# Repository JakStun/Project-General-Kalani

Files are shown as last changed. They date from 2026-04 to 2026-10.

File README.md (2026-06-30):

# Project-General-Kalani-V1

A talking and moving bust of an ST-series military strategic analysis and tactics droid serving the Confederacy of Independent Systems.

## Warning

* The neck joint is currently non-functional.

## Architecture Preview

```
User → Microphone → Raspberry Pi → Server → Response → Speaker
```

## Components

* Raspberry Pi 4 (4 GB)
* 3× RGB LED Module (7× NeoPixel WS2812)
* Adafruit I2S MEMS Microphone Breakout – SPH0645LM4H
* JBL Speaker
* LD2410C Human Presence Sensor (HLK-LD2410C)
* PCA9685 Servo Controller
* 2× Waveshare MG90S Micro Servos
* MG996R Servo
* External battery capable of powering the servos
* Dupont cables (10 cm, 20 cm, 30 cm, and 40 cm)

### Stores

* https://rpishop.cz
* https://www.drotik-elektro.sk

---

## Head

* All parts were printed on a Prusa Mini+.
* The parts were sanded using 120 → 240 → 320 → 600 grit sandpaper.
* Before using the 320 and 600 grit sandpaper, I applied a thin coat of Modulan 101 wood filler (purchased from Hornbach). It creates a smooth surface, hides the visible 3D printing layers, dries quickly, and does not chip off. Need to add little bit of water and mix it up.

### Filaments

* Prusament PETG Pigment White
* Buddy3D PLA White
* PolyTerra PLA White

### Stores

* https://www.prusa3d.com

* https://www.3djake.sk

* Printing all components took approximately three weeks. (It could have been faster—I wasn't printing continuously.)

* Approximately 1.5 spools of filament were used.

---

## Paints

* MASTON Plastic Primer
* MASTON Metallic Black
* MASTON Metallic Silver

### Store

* https://www.hornbach.sk

---

## Updates

Progress photos can be found in the `updates` folder.

---

## Project Preview

<p align="center">
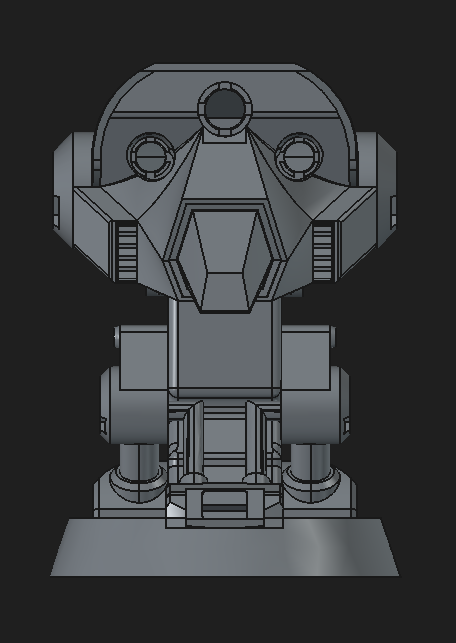
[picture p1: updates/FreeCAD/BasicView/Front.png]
Project Preview
  
</p>

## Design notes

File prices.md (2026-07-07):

# Cost of this project:

- Servos: 26 e (MG90S 180, MG996 180)
- MIC: 18 e (I bought second one for stereo and as a backup)
- Wiring: ~ 5 e
- Sensors: 30 e (LD2410, LD2410C, LD2450) (one LD2410C sensor self-combusted for some reason, had to buy new one...)
- RPi Camera V2: 16.5 e (testing human recognition)
- Adafruit 4 Ω 3 W Speakers - 10 e
- MAX98357 I2S mono amplifier 3W - 10 e (2x)
- LEDS: ~ 20 e (various types)

- TOTAL COST: 135.5 euros

- price is even higher though, these are just things I needed to buy. 

Components used, but not listed: 
- RPi 4 4GB (variable price nowadays)
- microSD 32GB (~10-15 euros)
- JBL Flip 3 (???)
- Old chinese powerbank (???)
- micro soldering station + other helper components (~90 euros)

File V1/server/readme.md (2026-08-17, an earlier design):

# Lucrehulk

- brain of all operations that require thinking/analysis

Run this command if you want all devices on local network to send requests:
```uvicorn main:app --host 0.0.0.0 --port 8000```

## Installation:

Tricky install-> torch (check newer versions), for this project I used: torch==2.6.0+cu124
Install it like this:  ```python.exe -m pip install torch==2.6.0+cu124 torchaudio==2.6.0+cu124 --index-url https://download.pytorch.org/whl/cu124```

For faster-wisper to work you need to have Visual Studio Build Tools for C++ installed (https://visualstudio.microsoft.com/visual-cpp-build-tools/)
Only then install: ```pip install "faster-whisper==1.2.1"```

After these are installed, install: ```pip install -r requirements.txt```

CUDA Tests (if available):
```python -c "import torch; print(torch.__version__); print(torch.version.cuda); print(torch.cuda.is_available()); print(torch.cuda.get_device_name(0))"```

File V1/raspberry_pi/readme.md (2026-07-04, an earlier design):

# V1 - Chilion Mahlon

## Full Cycle Preview:

```
I.   Human comes in front of Servitor (< 55 cm)

II.   Servitor activates itself, because it listens to LD2410S radar, that uncovers every movement in front of it:
        - servo moves head into 'awake' position
        - LEDs activate through startup  animation
        - MIC is set to active (NOT recording yet)
        - Optional: Servitor says something along these lines: At your service, Your word is my command...

III.  Human speaks Servitors name, thus activating MIC -> LEDs change color to Listening Mode

IV.   After humans request is recorded (human stops speaking and there is a slight/noticable pause), servitor sends their request for wisdom to Lucrehulk (Main Cogitator) and initiates Processing Mode, LEDs change to signal change

V.    Lucrehulk processes request for knowledge and returns appropriate answer to servitor (for more knowledge about Lucrehulk seek server folder)

VI.   Servitor spreads the unknown misterious knowledge to the keen listener and initiates Preaching Mode, again LEDs indicate this change

VII.  Human, satisfied with this new wisdom leaves servitor

VIII. After sensing no activity for a long time (~5 mins) Servitor starts 'sleep' funcs to preserve power and prepares itself for slumber: 
        - servo moves to 'sleep' position
        - LEDS start to jitter and at the end shut down
        - MIC is set to off
```

---

## Before launching code (Cerebrum.py):

- Interface Options (```sudo raspi-config```):
    - enable I2S (needed for MIC, it's not here anymore on newer version, just change config.txt)
    - enable I2C (needed for PCA9685)
    - enable SPI (needed for LED Control)
    - Serial Port (needed for LD2410 sensor):
        - disable ligin shell over serial
        - enable serial hardware

- MIC Configuration setup:
    I. ```sudo nano /boot/firmware/config.txt```
    II. Add/uncomment:
        - ```dtparam=i2s=on```
        - ```dtoverlay=googlevoicehat-soundcard```
    III. sudo reboot
    IV. Check if MIC is recognised and record test audio:
        - ```arecord -l```
        - ```arecord -D hw:3,0 -f S32_LE -r 48000 -c2 test.wav``` (if it doesn't work change hw:...,... -> maybe different port, can be seen by using func above)
        - speak into MIC
        - Ctrl+C -> stop recording
        - test.wav is created in /pi

- Speaker Configuration setup (JBL Flip):
    I. ```sudo systemctl start bluetooth```
    II. ```sudo systemctl enable bluetooth```
    III. ```bluetoothctl``` -> inside it:
        ```power on```
        ```agent on```
        ```default-agent```
        ```scan on``` -> search for XX:XX:XX:XX:XX:XX JBL Flip 3 (don't forget to start bluetooth on speaker aswell)
        ```pair XX:XX:XX:XX:XX:XX``` -> after success, should also see a popup: connection successful
        ```trust XX:XX:XX:XX:XX:XX```
        ```connect XX:XX:XX:XX:XX:XX```
        ```exit```
        
    IV. ```pactl list short sinks or wpctl status``` (depends on system) -> verify audio output, should be already default audio output (has * before name)
    V. ```speaker-test -c2``` or ```pw-play /usr/share/sounds/alsa/Front_Center.wav``` -> you should a stomp sound

    - if there is an error in bluetoothctl, check:
        - ```sudo systemctl status bluetooth --no-pager```
        - ```rfkill list```
        - ```hciconfig -a```
        - ```sudo rfkill unblock bluetooth```
        - ```sudo systemctl restart bluetooth```
        -> try running ```bluetoothctl``` and its commands again, should work now

---

## Installing new packages:

- WRONG APPROACH: sudo pip install --break-system-packages ... -> can break system
- CORRECT APPROACH: .venv (more stable) -> pip install ...

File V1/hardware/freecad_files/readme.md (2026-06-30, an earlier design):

##Warning:
-> FreeCAD files (for prototype and V1) are unfortunately corrupted for FreeCAD 1.1 and can't be opened without getting 10s of errors and warnings
-> They were designed in FreeCAD 1.0.1 - stable to open in this version

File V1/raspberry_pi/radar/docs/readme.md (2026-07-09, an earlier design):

During development, I've tried multiple Hi-Link radar sensors, here are links to offical drives
Only sensor I didn't try out was LD2461 (couldn't find it anywhere to buy it), seems interesting...

LD2410:
https://drive.google.com/drive/folders/1lCQv3mfHJ3XKXzweeHPFnJ_8_D_EWEKk

LD2410B:
https://drive.google.com/drive/folders/16zI-fium_BZeP08EyQke0rWp0BJTMvw3

LD2410C:
https://drive.google.com/drive/folders/1ypOlacBmmFXY6lDQ0f1hEJFmczNe-0WG

LD2450:
https://drive.google.com/drive/folders/1kTt0Z3hjKKrIF3OCIDGdwQ4KotDJ8SGA

LD2461:
https://drive.google.com/drive/folders/14_KgZpL4Th2LTRuq_W0X_ePjHu_Z6lcS

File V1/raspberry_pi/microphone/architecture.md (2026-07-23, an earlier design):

# Microphone Architecture

Used MIC: Adafruit I2S MEMS microphone breakout - SPH0645LM4H

```
microphone_control.py   -> main Controller for mic
recorder.py             -> captures PCM frames
vad.py                  -> voice activity detection
wakeword.py             -> OpenWakeWord wrapper
audio_buffer.py         -> ring buffer
```

Idea: 
First detect speech -> wake word - for that to work, I need MIC to record from the moment the robot is 'up'
    - this will be handled by recorder.py -> returns PCM frames (~ 33 frames per second)

Because of my beginner skills I needed to mostly rely on AI...
Nevertheless I read the docs to each library I used in MIC architecture

docs:
- https://python-sounddevice.readthedocs.io/en/0.5.3

0 vc4-hdmi-0: MAI PCM i2s-hifi-0 (hw:0,0), ALSA (0 in, 2 out)
1 bcm2835 Headphones: - (hw:2,0), ALSA (0 in, 8 out)
2 snd_rpi_googlevoicehat_soundcar: Google voiceHAT SoundCard HiFi voicehat-hifi-0 (hw:3,0), ALSA (2 in, 2 out)
3 sysdefault, ALSA (0 in, 128 out)
4 hdmi, ALSA (0 in, 2 out)
5 default, ALSA (0 in, 128 out)

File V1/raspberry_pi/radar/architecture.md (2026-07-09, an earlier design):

# Radar Architecture

- Used sensors: ```Hi-Link LD2410, LD2410C, LD2450```

- Pros:
    - Very Good/easy to use packages in python for operating these sensors (aio-ld2410...)
    - Easy wiring and RPi operating
    - Cheap

- Cons:
    - I needed to tinker with them alot (took me ~2 weeks to setup it corectly for this project)
    - at least in my case, one LD2410C unexpectedly burned down during testing, even though it was wired 100% correctly (no external power supply, everything was wired into RPi 4 (GND, 5V, RX, TX))

- Idea:
    - radar_control.py -> first thing that is called in cerebrum.py (after init callibration), will handle human detection
        - person walks to servitor (<55 cm, therefore I need to disable some gates in sensor and change moving threshold and static threshold for activa gates)
        - sensor sends signal to cerebrum -> which activates servitor
        - after person leaves (or there is no movement), sensor sends signal to cerebrum to shut down itself

    - PROBLEMS:
        - after shutting down, sensor sees this procedure -> sends signal to activate again -> infinite loop
            - FIX - filter out any movement (moving and static alike) that is very close to servitor (<30 cm), seems working 90% of times
        - I put my chair in front of the servitor (<50 cm) -> after I leave servitor activates itself, even though there is no one in front of it
            - FIX - instead of using detection_distence in if statement that decides whether there is someone in front of servitor, use moving_distance (makes sense, took me too long to come up with this fix...)

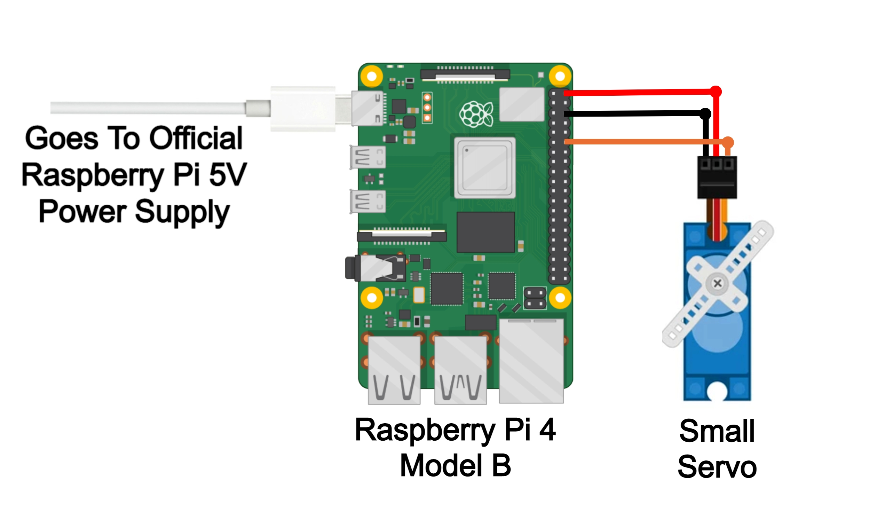
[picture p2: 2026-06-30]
V2/FreeCAD/Plans/Completed_Schematic_No_External_Power.webp

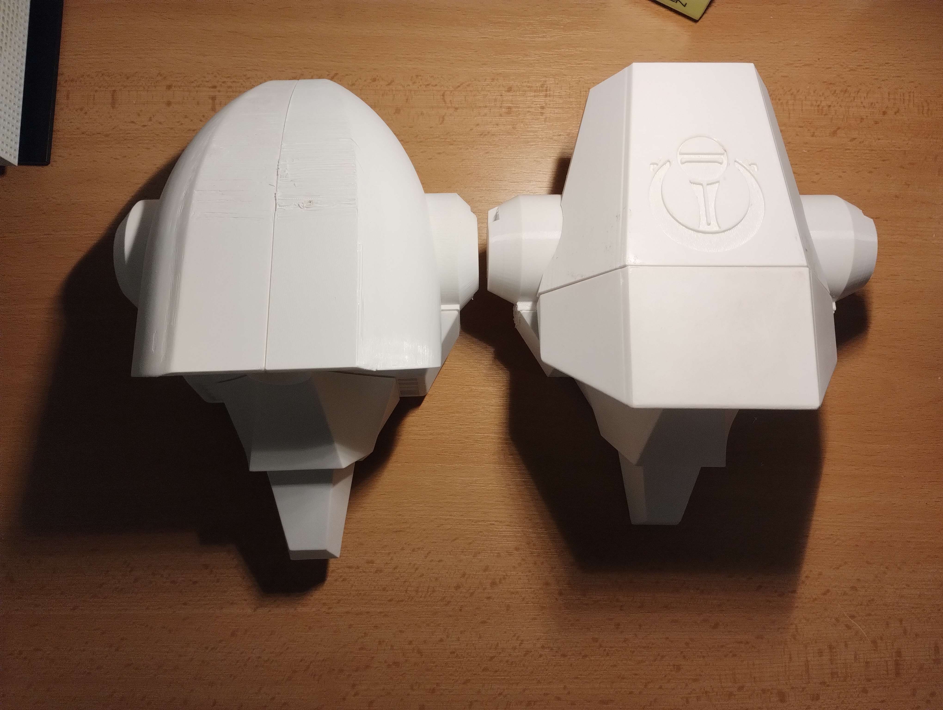
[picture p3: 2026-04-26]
updates/Progress/V1-Protoype-Comparison-Top.jpg

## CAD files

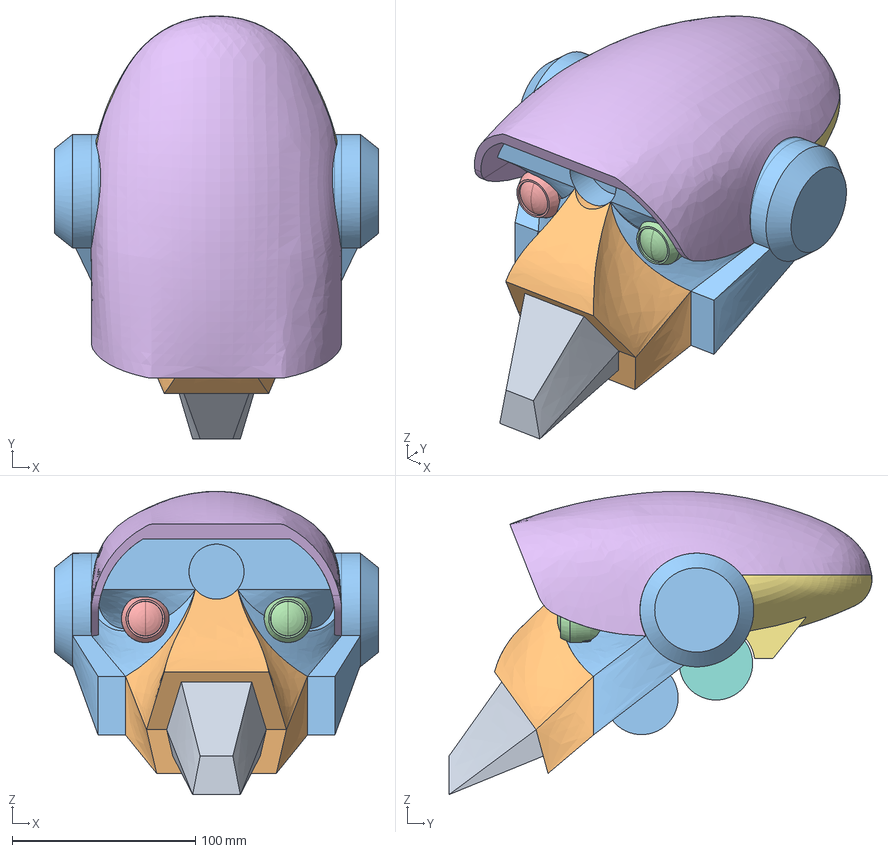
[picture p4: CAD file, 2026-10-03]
V2/FreeCAD/Head/MainHead-2.2.FCStd
176.9 x 230.7 x 165.4 mm
RostrumFullSolidCopy
GenaeCopy
MaxillaCopy
OculusDexter2.2.2
OculusDexter2.2.001
UpperCroniumCopy
LowerCroniumCopy
NeckJointCopy

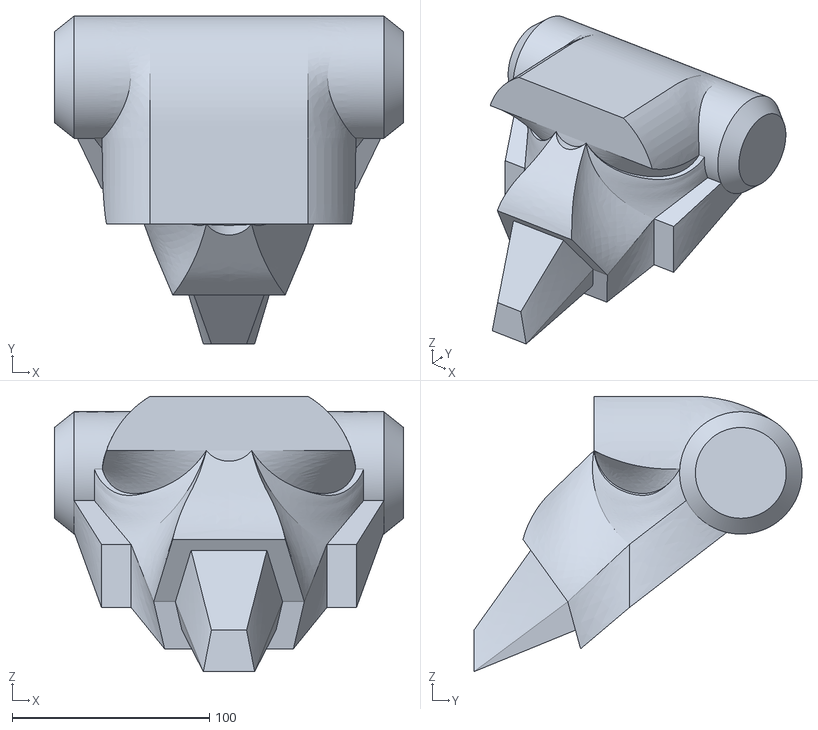
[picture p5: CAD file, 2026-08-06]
V2/FreeCAD/Head/stl/MainHead-2.1-fronttest.stl
176.9 x 166.2 x 139.5

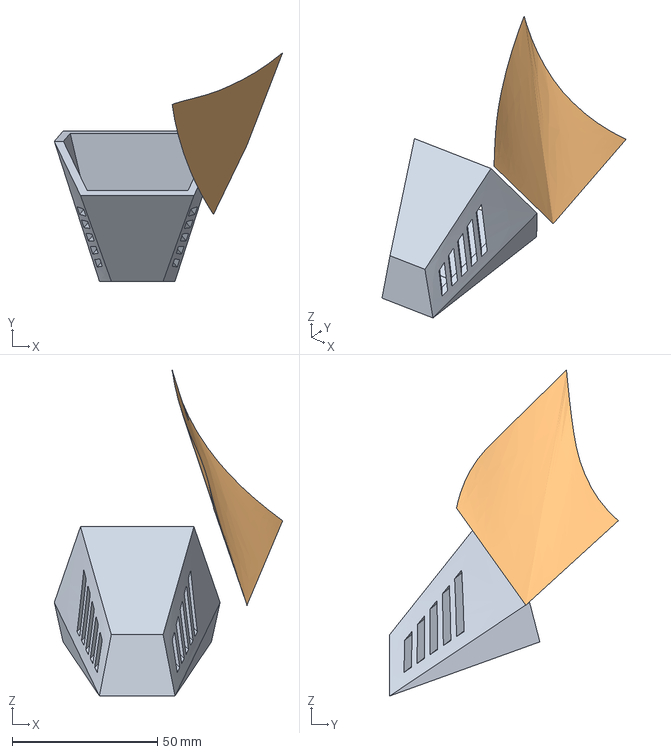
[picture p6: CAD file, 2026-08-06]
V2/FreeCAD/Head/MainHead-2.1.FCStd
78.5 x 78.6 x 112.0 mm
Rostrum
Ruled_Surface010

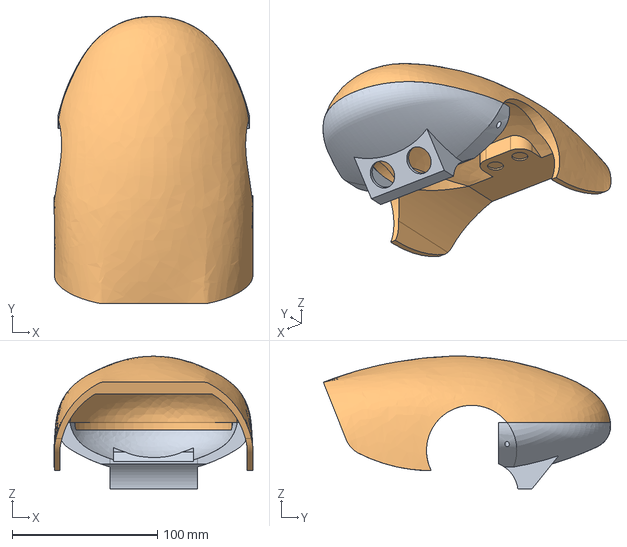
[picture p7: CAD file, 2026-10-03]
V2/FreeCAD/Head/Cronium/UpperCronium-2.2.1.FCStd
136.8 x 197.5 x 91.3 mm
LowerCroniumCopy-2.2.1.2

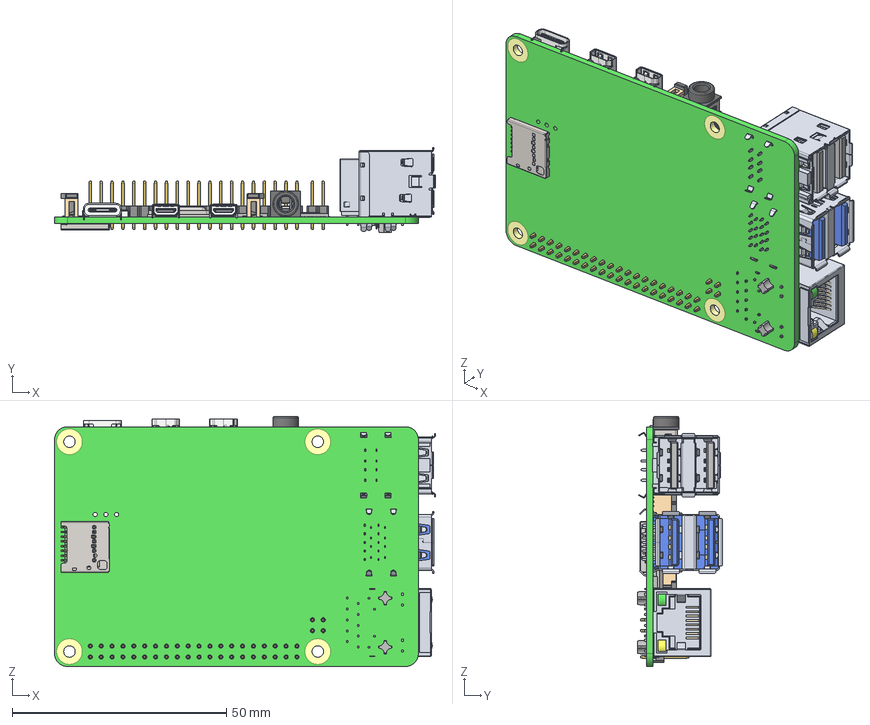
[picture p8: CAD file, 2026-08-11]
V2/FreeCAD/Head/ExternalFiles/raspberry-pi-4-model-b/Raspberry Pi 4 Model B.step
89.0 x 19.9 x 58.4 mm
PCB, RPi4ModelB
Broadcom BCM2711B0 CPU, RPi4ModelB
2.54 mm DUPONT MALE PIN HEADER, POE, 2X2, RPi4ModelB
2.54 mm DUPONT MALE PIN HEADER, IO, 2X20, RPi4ModelB
Camera Connector, RPi4ModelB
Microphone Plug, RPi4ModelB
Display Connector, RPi4ModelB
Gigabit Ethernet Port, RPi4ModelB
Female Micro HDMI Connector, RPi4ModelB x 2
Female USB Type C Connector, RPi4ModelB
2X USB3.0 PORTS, RPi4ModelB
91D77 D9WHV 778K, 4 GB LPDDR4 SDRAM, RPi4ModelB
Cypress CYW43455 Wireless Module Cover, RPi4ModelB
SD Card Slot, RPi4ModelB
VIA VL805 PCIe USB 3.0 controller, RPi4ModelB
2X USB2.0 PORTS, RPi4ModelB
Broadcom BCM54213PE Gigabit Ethernet Transceiver, RPi4ModelB
MxL7704 Universal PMIC, RPi4ModelB

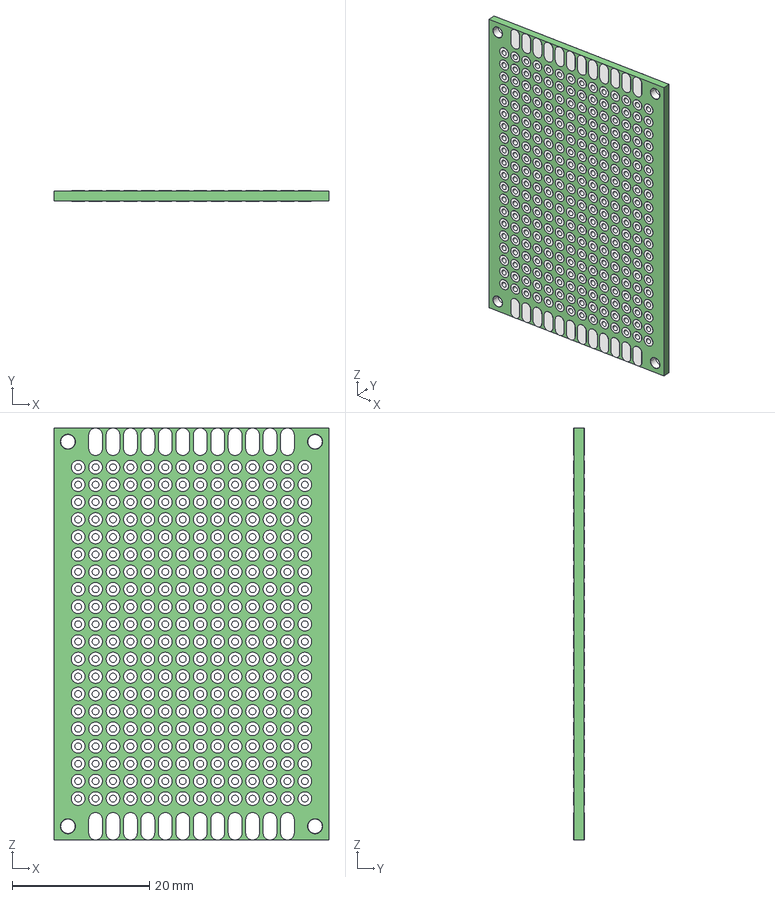
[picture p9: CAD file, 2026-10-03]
V2/FreeCAD/Head/ExternalFiles/Universal_board_40x60mm.stp
40.0 x 1.60 x 60.0 mm
Universal_board_40x60mm-prt0
Universal_board_40x60mm-prt1
Universal_board_40x60mm-prt2
Universal_board_40x60mm-prt3
Universal_board_40x60mm-prt4
Universal_board_40x60mm-prt5
Universal_board_40x60mm-prt6
Universal_board_40x60mm-prt7
Universal_board_40x60mm-prt8
Universal_board_40x60mm-prt9
Universal_board_40x60mm-prt10
Universal_board_40x60mm-prt11
Universal_board_40x60mm-prt12
Universal_board_40x60mm-prt13
Universal_board_40x60mm-prt14
Universal_board_40x60mm-prt15
Universal_board_40x60mm-prt16
Universal_board_40x60mm-prt17
Universal_board_40x60mm-prt18
Universal_board_40x60mm-prt19
Universal_board_40x60mm-prt20
Universal_board_40x60mm-prt21
Universal_board_40x60mm-prt22
Universal_board_40x60mm-prt23
Universal_board_40x60mm-prt24
Universal_board_40x60mm-prt25
Universal_board_40x60mm-prt26
Universal_board_40x60mm-prt27
Universal_board_40x60mm-prt28
Universal_board_40x60mm-prt29
Universal_board_40x60mm-prt30
Universal_board_40x60mm-prt31
Universal_board_40x60mm-prt32
Universal_board_40x60mm-prt33
Universal_board_40x60mm-prt34
Universal_board_40x60mm-prt35
Universal_board_40x60mm-prt36
Universal_board_40x60mm-prt37
Universal_board_40x60mm-prt38
Universal_board_40x60mm-prt39
Universal_board_40x60mm-prt40
Universal_board_40x60mm-prt41
Universal_board_40x60mm-prt42
Universal_board_40x60mm-prt43
Universal_board_40x60mm-prt44
Universal_board_40x60mm-prt45
Universal_board_40x60mm-prt46
Universal_board_40x60mm-prt47
Universal_board_40x60mm-prt48
Universal_board_40x60mm-prt49
Universal_board_40x60mm-prt50
Universal_board_40x60mm-prt51
Universal_board_40x60mm-prt52
Universal_board_40x60mm-prt53
Universal_board_40x60mm-prt54
Universal_board_40x60mm-prt55
Universal_board_40x60mm-prt56
Universal_board_40x60mm-prt57
Universal_board_40x60mm-prt58
Universal_board_40x60mm-prt59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

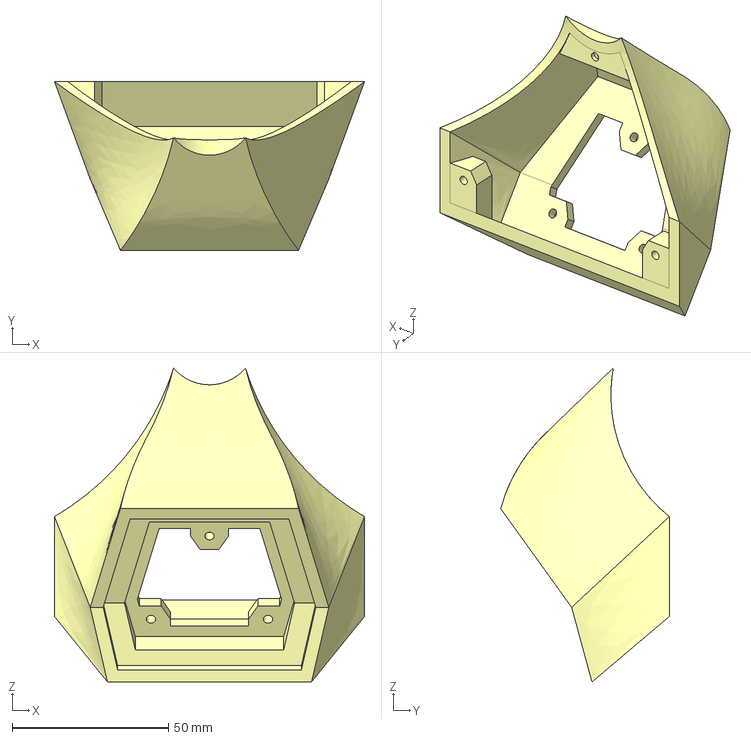
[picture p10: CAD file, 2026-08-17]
V2/FreeCAD/Head/Genae/Genae-2.2.1.step
99.2 x 53.9 x 100.4 mm

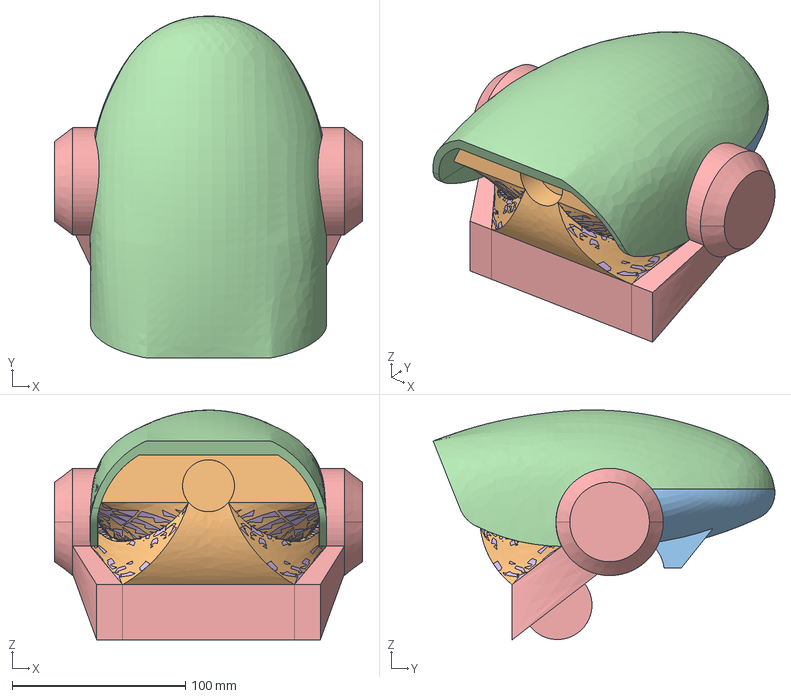
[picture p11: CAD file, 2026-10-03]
V2/FreeCAD/Head/Maxilla/LowerMaxilla-2.2.1.FCStd
178.0 x 197.5 x 132.9 mm
LowerCroniumCopy
UpperCroniumCopy
BottomMaxilla001

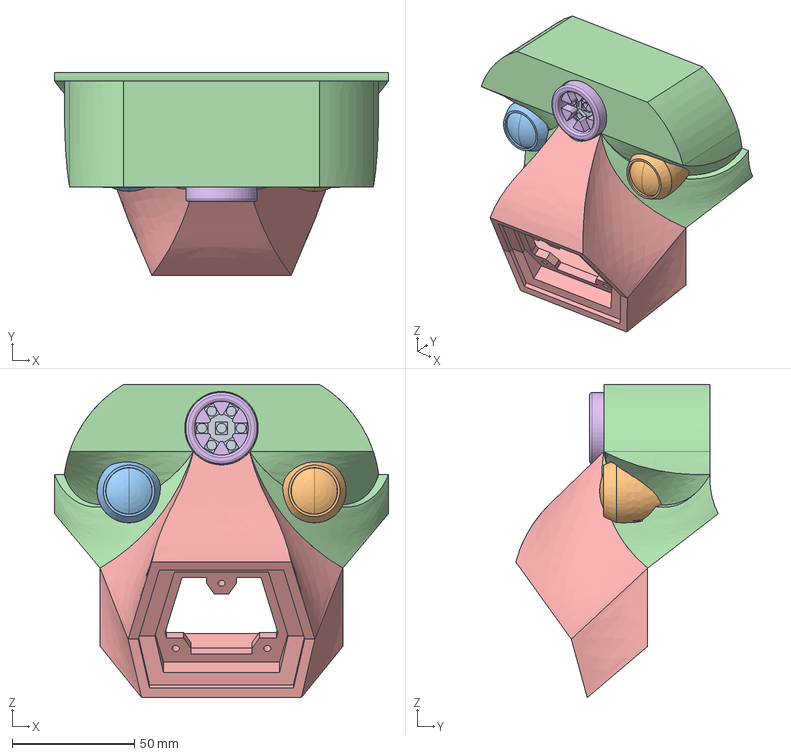
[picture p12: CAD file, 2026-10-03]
V2/FreeCAD/Head/Oculi/OculusCyclopis-2.2.1.FCStd
136.4 x 82.7 x 127.9 mm
M2-Nut
M2-Nut013
M2-Nut016
M2-Nut017
M2x10-Screw
M2x10-Screw003
M2x10-Screw008
M2x10-Screw009
RGBLEDModuleNeopixel
OculusDexter2.2.2-SimpleCopy
OculusDexter2.2.2-SimpleCopy001
UpperMaxillaSolid
GenaeCopy-2.2.1

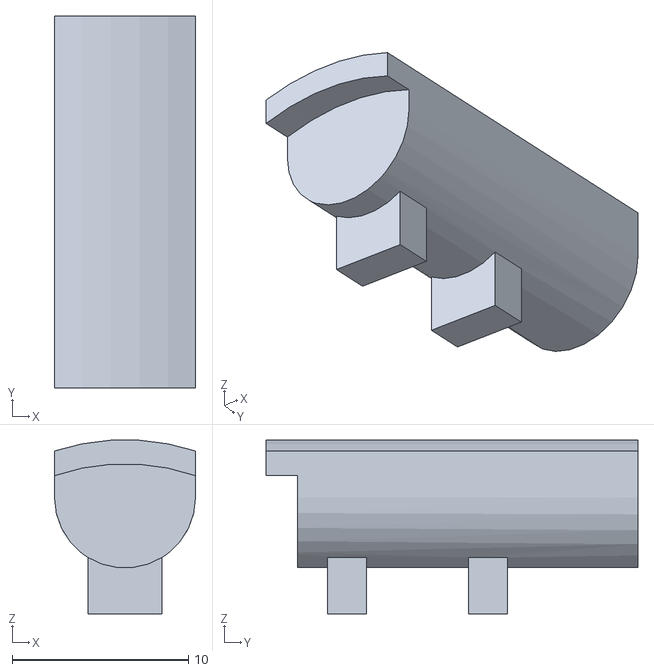
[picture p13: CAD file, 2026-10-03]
V2/FreeCAD/Head/Oculi/stl/OculusDexter-2.2.2-MeshedUpperAttacher.stl
8.00 x 21.1 x 9.85

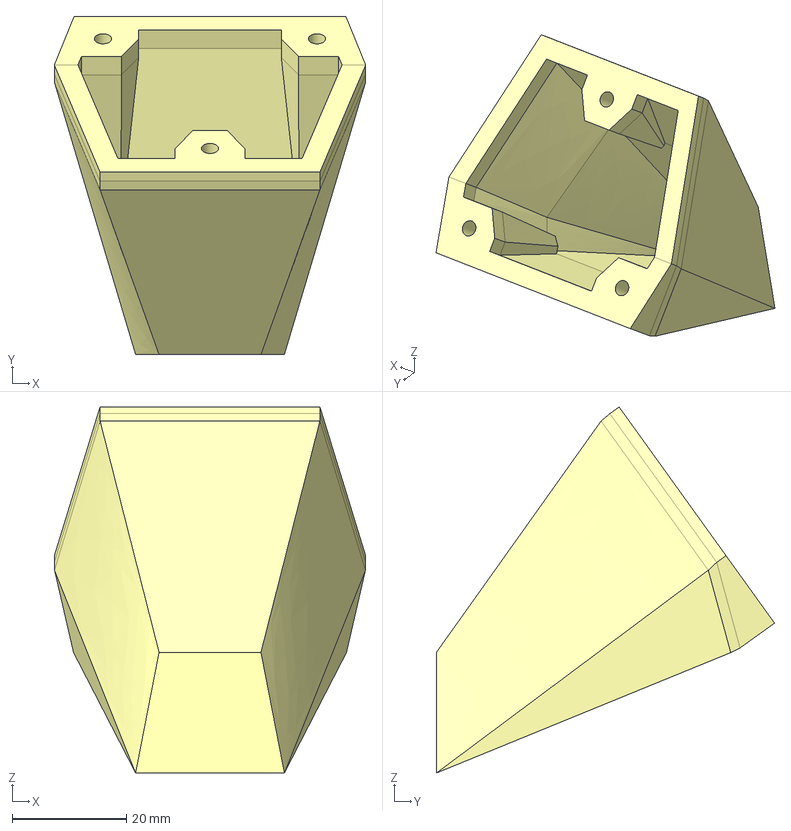
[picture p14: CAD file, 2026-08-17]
V2/FreeCAD/Head/Rostrum/Rostrum-2.2.1.step
54.4 x 59.1 x 64.0 mm

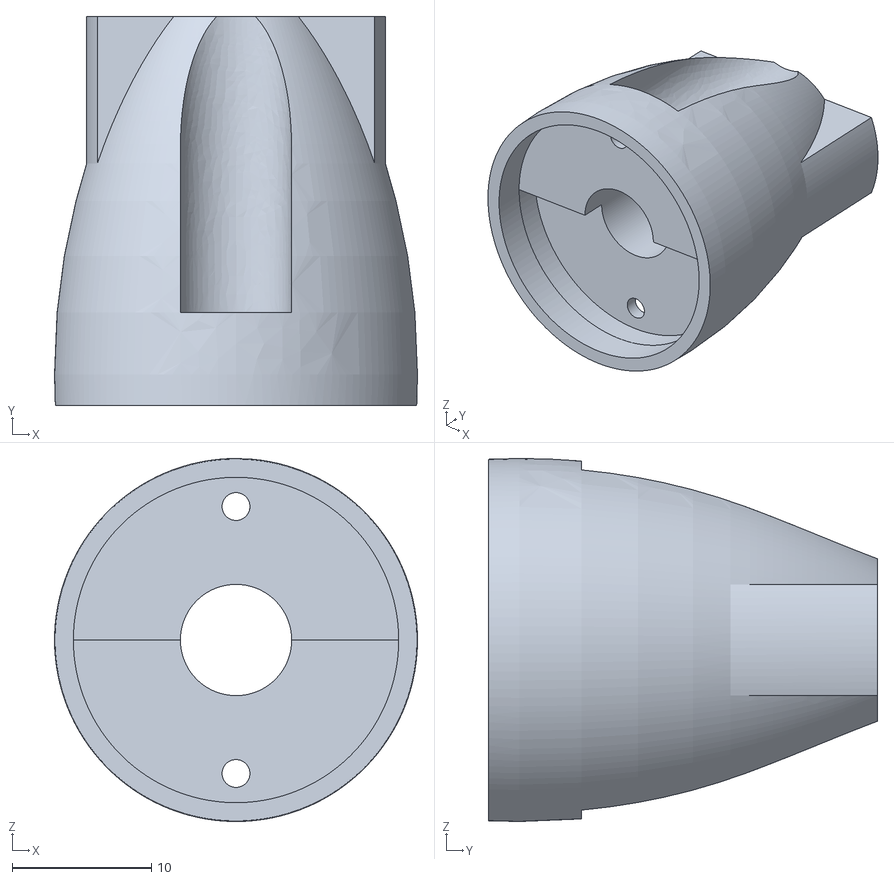
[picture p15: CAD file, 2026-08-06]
V2/FreeCAD/Head/Tests/OculusDexter-test-2.2-RearOD.stl
26.1 x 28.0 x 26.1

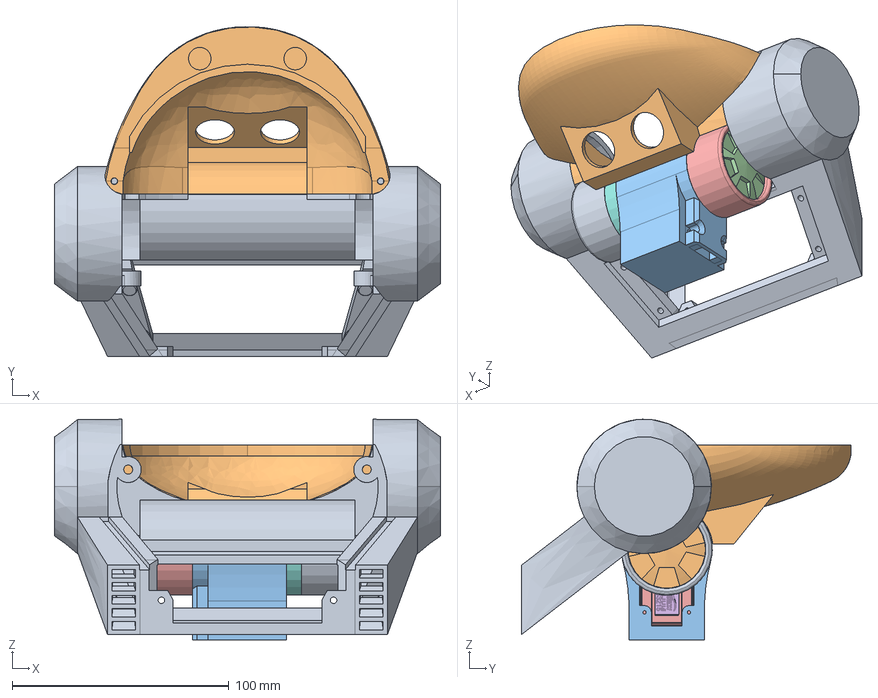
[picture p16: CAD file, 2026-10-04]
V2/FreeCAD/Pedestal/UpperNeck/UpperNeck-2.1.1.FCStd
178.0 x 152.0 x 101.7 mm
BottomMaxilla-2.2.2.2
LowerCroniumCopy-2.2.1.1
Middle
Top
Bottom
Spox Molex 3pin v1
Spox Molex 3pin v002
Spox Molex 3pin v003
Spox Molex 3pin v004
Spox_Molex_3pin_002
Spox_Molex_3pin_003
Spox_Molex_3pin_004
Spox_Molex_3pin_005
Freetech_sts3215
M2x6-Vis001
M2x6-Vis
M2x4-Vis001
M2x4-Vis
GE_27
\X2\91D15C5E823576D8FF089A7152A8FF09\X0\ v2
\X2\91D15C5E823576D8FF084ECE52A8FF09\X0\ v2
M3x4-Vis
M3x4-Vis001
RightUpperJointServoAttacher
RightUpperOuterJoint
RightUpperInnerJoint
UpperJointHolder
LeftUpperInnerJoint
LeftUpperJoint

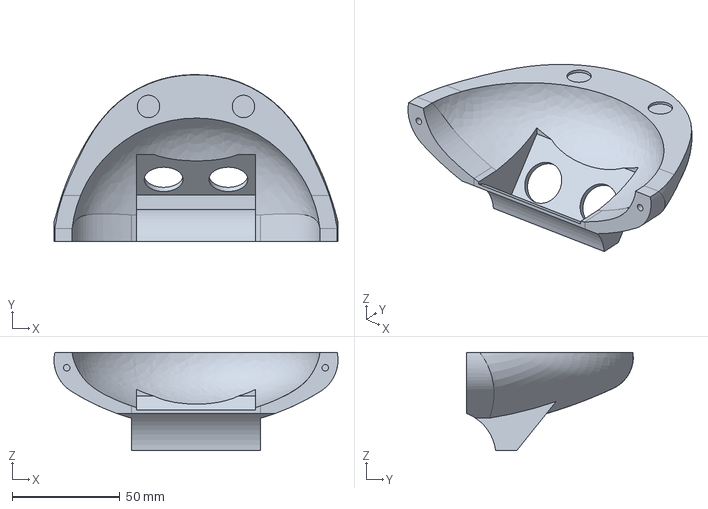
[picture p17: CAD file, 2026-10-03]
V2/FreeCAD/Head/Cronium/LowerCronium-2.2.1.FCStd
131.6 x 77.2 x 45.6 mm

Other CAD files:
V2/FreeCAD/Head/Rostrum/stl/Rostrum-2.2.1-RostrumFinalSolid.stl
V2/FreeCAD/Head/ExternalFiles/raspberry-pi-4-model-b/RaspPi-4B.FCStd
V2/FreeCAD/Head/ExternalFiles/Universal_board_20x80mm.stp
V2/FreeCAD/Head/Oculi/OculusDexter-2.2.2.step
V1/hardware/freecad_files/v1/ExternalParts/mg90s-micro-servo/M90S_ali.step
V1/hardware/freecad_files/v1/ExternalParts/mg90s-micro-servo/MG90S_arm01.step
V1/hardware/freecad_files/v1/ExternalParts/mg90s-micro-servo/mg90_ali/M90S_ali.FCStd
V1/hardware/freecad_files/v1/ExternalParts/mg90s-micro-servo/mg90_ali/MG90S_bras_01.FCStd
V1/hardware/freecad_files/v1/ExternalParts/mg90s-micro-servo/mg90_ali/mg90s_with_arm.FCStd
V1/hardware/freecad_files/v1/ExternalParts/mg90s-servo/MG90S ARM.step
V1/hardware/freecad_files/v1/ExternalParts/mg90s-servo/MG90S NO TEETH.step
V1/hardware/freecad_files/v1/ExternalParts/mg90s-servo/MG90S TEETH.step
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

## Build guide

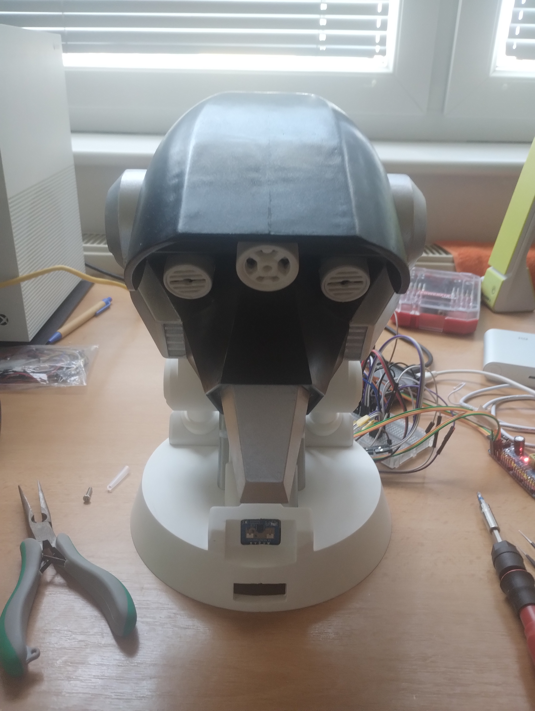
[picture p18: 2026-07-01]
updates/Progress/V1-Initial-Assembly-5.jpg

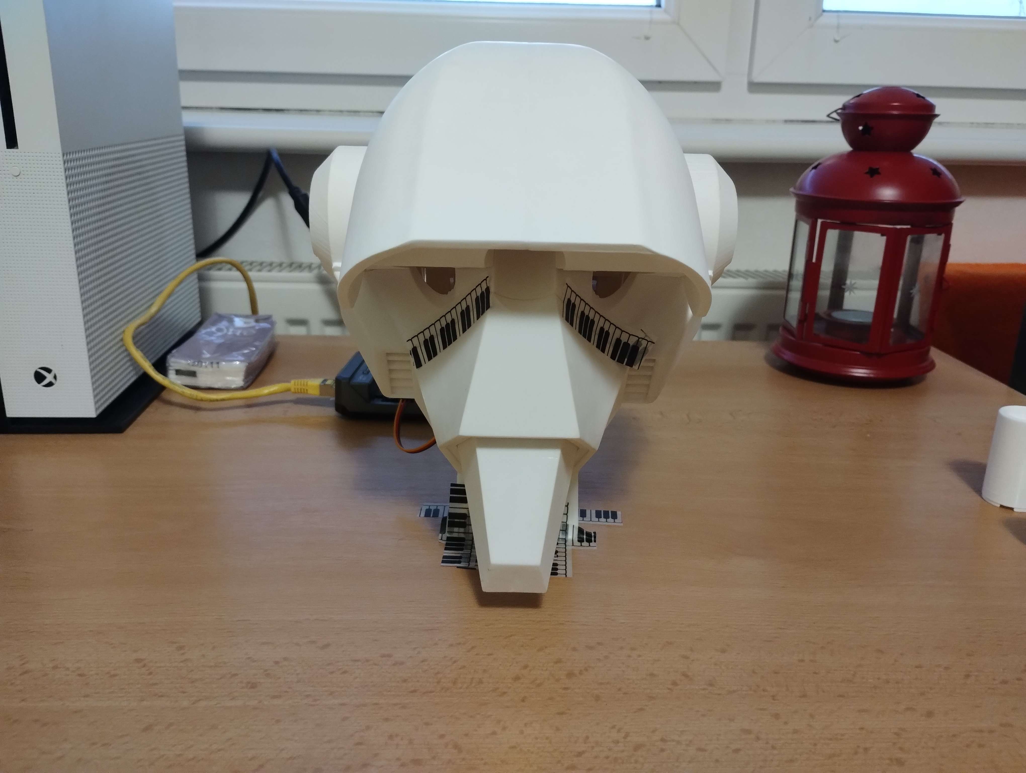
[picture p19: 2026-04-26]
updates/Progress/V1-initial-Assembly-2.jpg

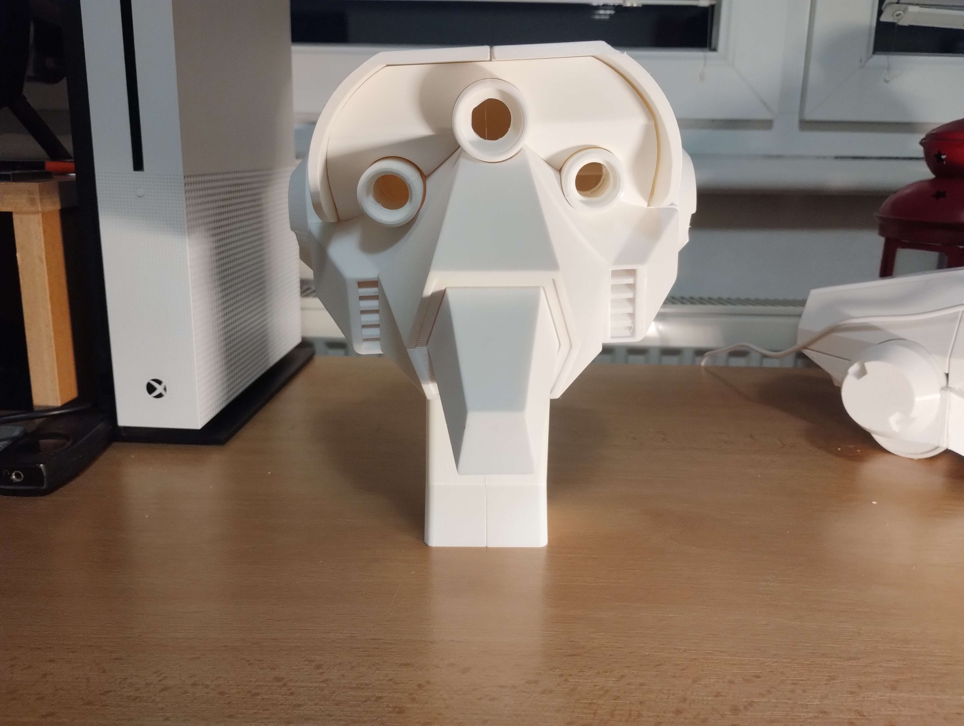
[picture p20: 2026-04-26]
updates/Progress/V1-Head-NeckPrototype-Assembly.jpg

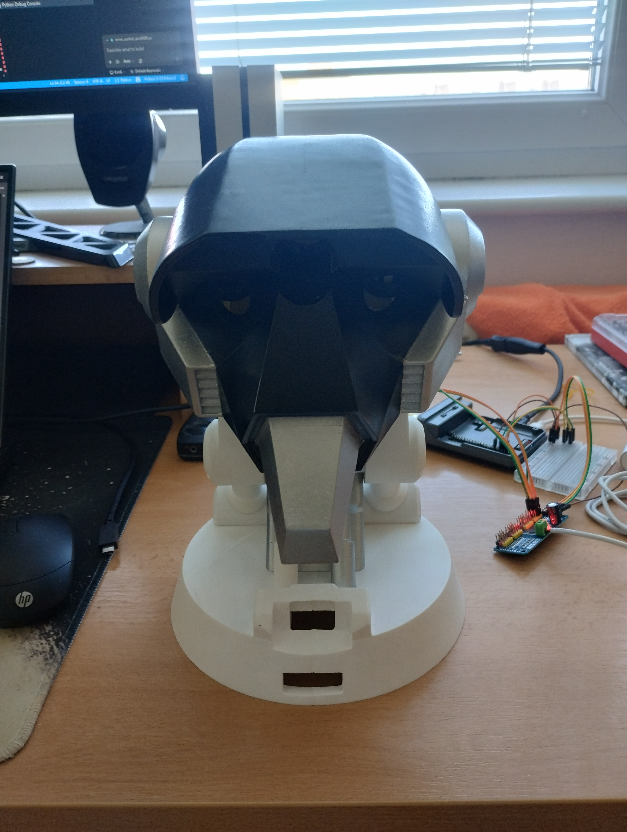
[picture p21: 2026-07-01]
updates/Progress/V1-Initial-Assembly-4.jpg

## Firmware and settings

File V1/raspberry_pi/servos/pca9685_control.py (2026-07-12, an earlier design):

import asyncio
import board 
import busio 

from math import pi, cos 
from logging import getLogger
from adafruit_servokit import ServoKit 

class ServoControlPCA9685: 
    RIGHT_CHANNEL = 0 
    LEFT_CHANNEL = 1 

    def __init__(self) -> None: 
        self.logger = getLogger("main") 
        
        i2c = busio.I2C(board.SCL, board.SDA) 
        
        self.kit = ServoKit(
            channels=16, 
            i2c=i2c,
        ) 
        
        #TODO: Calibrating pulse for SG90 servos, needs further testing 
        self.kit.servo[self.RIGHT_CHANNEL].set_pulse_width_range(
            500, 
            2500
        ) 
        
        
        self.kit.servo[self.LEFT_CHANNEL].set_pulse_width_range(
            1000,
            2000
        ) 
        
        self.current_angle = 0 
        
        self._set_init_angle() 

    async def calibrate(self) -> None: 
        with open("servo_pos.txt") as f: 
            last = float(f.read()) 
        
        await asyncio.sleep(1) 
        
        if last > -29: 
            try: 
                await self.move(-30) 
                self.logger.info("[SERVO] Calibrating SLUMBER POSITION successful") 
            except Exception: 
                self.logger.exception("[SERVO] Failed to calibrate into SLUMBER POSITION") 
        else: 
            self.logger.info("[SERVO] Already in SLUMBER POSITION") 

    async def wake_animation(self) -> None: 
        self.logger.info("[SERVO] Servitors gears moving to awoken stature...") 
        
        await self.move(15) # TODO: experiment 
        await self.move(10, duration=0.5) 

    async def sleep_animation(self) -> None: 
        self.logger.info("[SERVO] Servitors gears moving to slumber stature...") 
        
        await self.move(-25) 
        await self.move(-30, duration=0.5) 

    async def move(self, target: float, duration: float = 2.5, steps: int = 50) -> None: 
        """ Moves servitor joints to set position <-90, 90> """ 
        self.logger.info(f"[SERVO] Moving to {target}° over {duration} secs") 
        start = self.current_angle 

        for step in range(steps + 1): 
            t = step / steps 
            eased = start + (target- start) * (0.5 - 0.5 * cos(pi * t)) 

            self._set_pair_angle(eased) 

            await asyncio.sleep(duration / steps) 

        self.current_angle = target 

        self._save_position() # disable PM output 

        self._detach() 

        self.logger.info("[SERVO] Moving procedure finished") 

    def _set_pair_angle(self, angle: float) -> None: 
        """ inside class -> -90 ... 90 servokit wants -> 0 ... 180 """ 
        right = 90 + angle 
        left = 90 - angle 

        self.kit.servo[self.RIGHT_CHANNEL].angle = right 
        self.kit.servo[self.LEFT_CHANNEL].angle = left 

    def _detach(self) -> None: 
        self.kit.servo[self.RIGHT_CHANNEL].angle = None 
        self.kit.servo[self.LEFT_CHANNEL].angle = None 

    def _save_position(self) -> None: 
        with open("servo_pos.txt", "w") as file: 
            file.write(str(self.current_angle)) 

    def _set_init_angle(self) -> None: 
        self.logger.info("[SERVO] Setting last position") 

        try:
            with open("servo_pos.txt") as f:
                last = float(f.read())

            self.logger.info(f"[SERVO] Loaded last position: {last}°")

        except Exception:
            last = 0

            self.logger.warning("[SERVO] Failed to load last position, setting 0°")

        self.current_angle = last

        self._set_pair_angle(last)

        self.logger.info("[SERVO] Last position set successfully")

if __name__ == "__main__":
    import time

    async def main():
        servo_control = ServoControlPCA9685()

        await servo_control.calibrate()

        # await servo_control.wake_animation()
        # await asyncio.sleep(1)
        # await servo_control.sleep_animation()
        # await servo_control.move(target=0)

        # time.sleep(10)

        while True:
            await servo_control.move(target=5, steps=30)
            time.sleep(2)

            await servo_control.move(target=-30, steps=100, duration=3)
            time.sleep(2)

    asyncio.run(main())

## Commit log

2026-03-07 prototype parts
    [back_ear__left_v1.stl, bigger_eye_v1.stl, bottom_front_v1.stl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]
2026-03-07 v1 parts
    [Beak.stl, BiggerEye.stl, BiggerEyeLid.stl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]
2026-03-14 added neck attacher and servo holder
    [NeckAttacher.stl, RightServoHolder.stl]
2026-03-16 added voice sample for training
2026-03-20 fixed issues regarding neck attachment
    [NeckAttacher.stl, RightServoHolder.stl]
2026-03-21 created llm class (not working)
    [config.py]
2026-04-05 added new voice samples
2026-04-26 updated eye design -> needed for RGB LED
    [BigEyeBack.stl, BigEyeFront.stl, BigEyeLid.stl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]
2026-05-04 changed components (mic, sensor)
2026-06-30 quick rpi code fix
    [cerebrum.py, pca9685_control.py]
2026-06-30 updated freecad parts (final for V1)
    [BigServoMechanism.FCStd, FixedGearMechanism.FCStd, FixedUpperGear.FCStd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]
2026-06-30 updated stl files (final for V1)
    [BackJoint.stl, BigEyeLid.stl, BigEyeLidNail.stl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]
